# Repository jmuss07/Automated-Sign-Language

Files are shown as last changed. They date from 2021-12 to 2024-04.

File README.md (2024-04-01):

# Automated Sign Language

## Table of Contents

- [Phase 1](#phase-1)
- [Phase 2](#phase-2)
- [Phase 3](#phase-3)
- [About Us](#about-us)

## Phase 1

Goals, Planning, etc.

**Description**: A robotic, anthropomorphic hand that can display the ASL alphabet and basic one-handed gestures.

**Test of Success**: Through the hand, using the ASL alphabet, a word can be transmitted, received, and interpreted in under two minutes.

**Proof of Concept**: [ASLAN robot](https://www.hubs.com/blog/theres-not-enough-sign-language-translators-so-these-students-3d-printed-a-humanoid-robot/) made by Uni. of Antwerp students.

Components of Antwerp:

- 16 servos
- 25 3D printed parts (139 hour print time)
- 3 motor controllers
- Arduino Due
- 10 hour assembly time
- Access to global database

| Recreatable | Unrealistic |
| --- | --- |
| Arm is 3D printed | 16 servos |
| Roughly human size | Able to learn |
| Multiple parts that assemble into the whole | Access to constantly updated local network of global signs |
| Finger and arm joints move individually | Network connected users can send messages that the hand interprets |

### What We Don't Know

- How to make a moveable finger joint.
- Typed input into letters, into hand sign. What's the process? (Library of servo movements? for each letter?).
- Turn speech into text that can be then inputted.
- Some signs and gestures require either unnatural movement, or a more complex process.
  - The signs for "z" and "j" require excessive movement of the arm.
  - Thumbs-up and thumbs-down require arm rotation.
  - etc.

### What We Need to Learn

- How to take audio (of speech), and turn it into a string interpretable by a microcontroller.
  - Speech-to-text (on raspberry pi?)
  - Parse and turn text into individual letters.
  - Turn the individual letters into commands for each part of the hand.
- How a synthetic joint can be controlled by a servo motor.
  - Finger joint(s)
  - Wrist! It has multiple directions of movement irl!
- How to use a raspberry pi (as a speech-to-text server) in coordination with an arduino (as a microcontroller).
  - USB out on raspi (raspberry pi) to arduino?
  - Pins on raspi to arduino?
  - etc?

### Work Delegation

| Category | Josie | Henry |
| --- | ----- | ----- |
| Speech-to-text | 65% | 35% |
| Finger & Wrist control | 35% | 65% |

_Note: These numbers and divisions are pretty arbitrary._

### Timeline

| Date  | Goal |
| ----- | --- |
| 12/17 | Planning finished, box & arm modeled, hand & stt (speech-to-text) started |
| 1/7 | Box finished, arm in final revisions, servo/hand issue solved, rudimentary stt established |
| 1/14  | Arm finished, hand being developed with servos, stt able to trigger servo |
| 1/21  | Hand being printed/in final revisions, full project assembled, stt finished |
| 1/28  | Physical project finished, troubleshooting |
| 2/4 | Final documentation finished, project submitted |

### Estimated Cost

| Item | Cost per Item | Quantity | Total Cost |
| --- | --- | --- | --- |
| Servo | $5.95 | 8 | $47.60 |
| 3D Printer Model Material | $2.43 / in³ | 8 in³ | $19.44 |
| 3D Printer Support Material | $4.76 / in³ | 1.5 in³ | $7.14 |
| 1/8" Acrylic Sheet | $2.65 / ft² | 9.5 ft² | $25.18 |
| Wire | $0.08 / ft | 6 ft | $0.48 |
| Panel-mount SPDT Switch | $0.95 | 1 | $0.95 |
| LED (Green or Red) | $0.16 | 1 | $0.16 |
| Arduino Uno/Metro | $24.95 | 1 | $24.95 |
| Arduino Prototyping Shield  | $11.49 | 1 | $11.49 |
| Raspberry Pi | $35.00 | 1 | $35.00 |
| | | **Final Estimated Cost**: | $172.39 |

Yes, this estimated cost is rather high. However, a lot of these materials are readily available already in the Sigma Lab, and can be re-used for future projects. If need be, $75 is available to purchase extra materials.

_Thanks to [Sigma Lab Wiki](http://wiki.chssigma.com/index.php?title=Sigma_Lab_Equipment_Costs) for the numbers._

### Parts and Uses

| Part | Use |
| --- | --- |
| Microphone | To pick up speech as audio. |
| Raspberry Pi | To run a speech-to-text server, and turn the audio into strings, and the strings into commands sent to the arduino. |
| Arduino | To control the servos. |
| Switch | To turn the whole unit on and off. |
| Arm Servos | To rotate the arm, and bend the wrist. |
| Hand Servos  | To control the individual fingers on the hand. |
| Elastic | To let the hand servos bend/extend the fingers on the hand. |

### Safety

- The base box will be made of acrylic, and have the weight of the arm on it. If any point has too much stress, the acrylic could break. This would cause sharp edges, so there's **danger of cuts**.
- If the whole arm will be able to rotate, and the fingers/wrist move quick, then there will be a lot of fast movement. If parts are not secured properly, there could be a **risk of parts flying off and hurting someone**.
- As the physical interaction with the arm would be minimal, the **risk for electrical shock is low**.
  **soldering**
- We will need to solder various wires, which has the **risk of fire and burns** if the soldering iron is not used correctly.

### Images

A basic sketch for how the tension of the front of the arm may look...

FrontOfArm

...And a similar sketch for the back of the arm!

BackOfArm

_Credit to [Benton House](https://github.com/jhouse53) for the arm._

## Phase 2

Milestone work (From research, to final work)

The OpenBionics Lab's ADA v1.1 hand has designs for exactly what we're doing. But, it's designed for different servos, and a custom PCB. If we use anything from it, adaptations need to be made.

[ADA v1.1 Datasheet](Images/Ada_v1_1_Datasheet.pdf)

[Open Bionics Lab](https://openbionicslabs.com/downloads)

Below, is documentation of a single makeshift finger. Designed with minimal 3D printing, so manufacturing time is low. Overall, the only 3D-printed parts are the dowels, which take all of 10 minutes.

Finger Video:

https://user-images.githubusercontent.com/71345201/172168732-d8e445a4-d9d3-42a7-b983-bf6e3092c325.mp4

Box Video:

https://user-images.githubusercontent.com/71345201/172168760-eeb97748-df77-4b64-b599-513adac0ddce.mp4

Now, it's time to move onto the design of the final hand. The ADA v1.1 hand is made of a lot of Ninjaflex, too much for our project's budget. The final phase 2 goal is to cut this down.

So, it seems that the files provided by Open Bionics Labs were meshes, which Onshape does not support the editing of. The next best option is to either print the entire hand as-is, or re-design the fingers. The re-design would use the original .stl files as reference.

[Mesh Issues Video](Videos\2022-02-25_MeshIssues-mp4.mp4)

## Phase 3

Phase 3 is the combination and culmination of our work on the hand, string interpretation, and multi-servo control. As of now, this will not be achieved by the February 25th deadline. February 25th 2022, which at the time of writing, is today.

That was written over 2 months ago. Now, work starts again. At the moment, we have the fingers printed! Turns out, the Blender files (included with the ADA v1.1 download) were editable. This means a much higher chance of completing this project.

But before we get into that, lets take a break from all of this CAD to talk about the coding side of the project!
 Code Video Part 1:
 
 [Josie Stuff 1 Video](/Videos/2022-03-01_JosieStuff-mp4.mp4)
 
 Code Video Part 2:
 
 [Josie Stuff 2 Video](/Videos/2022-03-01_JosieStuff-2-mp4.mp4)
 
**ASL_Functions (Code Library):**
```python
import board
import neopixel
import pwmio
import servo

dot = neopixel.NeoPixel(board.NEOPIXEL, 1)
dot.brightness = 0.1

def full_up(servoToActuate):
    servoToActuate.angle = 0
def full_down(servoToActuate):
    servoToActuate.angle = 180
def half_fold(servoToActuate):
    servoToActuate.angle = 90
def full_palm(servoToActuate):
    servoToActuate.angle = 180
def half_palm(servoToActuate):
    servoToActuate.angle = 90
def pointed_out(servoToActuate):
    servoToActuate.angle = 0
def half_out(servoToActuate):
    servoToActuate.angle = 45

pwm1 = pwmio.PWMOut(board.D3, duty_cycle=2**15, frequency=200)
pwm2 = pwmio.PWMOut(board.D4, duty_cycle=2**15, frequency=200)
pwm3 = pwmio.PWMOut(board.D5, duty_cycle=2**15, frequency=200)
pwm4 = pwmio.PWMOut(board.D6, duty_cycle=2**15, frequency=200)
pwm5 = pwmio.PWMOut(board.D7, duty_cycle=2**15, frequency=200)

thumb = servo.Servo(pwm1)
pointer = servo.Servo(pwm2)
middle = servo.Servo(pwm3)
ring = servo.Servo(pwm4)
pinky = servo.Servo(pwm5)

def neutral():
    full_up(thumb)
    full_up(pointer)
    full_up(middle)
    full_up(ring)
    full_up(pinky)

def sign_a():
    full_up(thumb)
    full_down(pointer)
    full_down(middle)
    full_down(ring)
    full_down(pinky)
    print("A")

def sign_b():
    full_palm(thumb)
    full_up(pointer)
    full_up(middle)
    full_up(ring)
    full_up(pinky)
    print("B")

def sign_c():
    half_out(thumb)
    half_fold(pointer)
    half_fold(middle)
    half_fold(ring)
    half_fold(pinky)
    print("C")

def sign_d():
    full_palm(thumb)
    full_up(pointer)
    full_down(middle)
    full_down(ring)
    full_down(pinky)
    print("D")

def sign_e():
    full_palm(thumb)
    half_fold(pointer)
    half_fold(middle)
    half_fold(ring)
    half_fold(pinky)
    print("E")

def sign_f():
    half_fold(thumb)
    half_fold(pointer)
    full_up(middle)
    full_up(ring)
    full_up(pinky)
    print("F")

def sign_g():
    full_up(thumb)
    full_up(pointer)
    full_down(middle)
    full_down(ring)
    full_down(pinky)
    print("G")

def sign_h():
    full_up(thumb)
    full_up(pointer)
    full_up(middle)
    full_down(ring)
    full_down(pinky)
    print("H")

def sign_i():
    half_fold(thumb)
    full_down(pointer)
    full_down(middle)
    full_down(ring)
    full_up(pinky)
    print("I")

def sign_j():
    half_fold(thumb)
    full_down(pointer)
    full_down(middle)
    full_down(ring)
    full_up(pinky)
    print("J")

def sign_k():
    full_up(thumb)
    full_up(pointer)
    full_up(middle)
    full_down(ring)
    full_down(pinky)
    print("K")

def sign_l():
    pointed_out(thumb)
    full_up(pointer)
    full_down(middle)
    full_down(ring)
    full_down(pinky)
    print("L")

def sign_m():
    full_palm(thumb)
    half_fold(pointer)
    half_fold(middle)
    half_fold(ring)
    full_down(pinky)
    print("M")

def sign_n():
    full_palm(thumb)
    half_fold(pointer)
    half_fold(middle)
    full_down(ring)
    full_down(pinky)
    print("N")

def sign_o():
    half_fold(thumb)
    half_fold(pointer)
    half_fold(middle)
    half_fold(ring)
    half_fold(pinky)
    print("O")

def sign_p():
    full_up(thumb)
    full_up(pointer)
    half_fold(middle)
    full_down(ring)
    full_down(pinky)
    print("P")

def sign_q():
    full_up(thumb)
    full_up(pointer)
    full_down(middle)
    full_down(ring)
    full_down(pinky)
    print("Q")

def sign_r():
    half_palm(thumb)
    full_up(pointer)
    full_up(middle)
    full_down(ring)
    full_down(pinky)
    print("R")

def sign_s():
    half_palm(thumb)
    full_down(pointer)
    full_down(middle)
    full_down(ring)
    full_down(pinky)
    print("S")

def sign_t():
    full_up(thumb)
    half_fold(pointer)
    full_down(middle)
    full_down(ring)
    full_down(pinky)
    print("T")

def sign_u():
    half_palm(thumb)
    full_up(pointer)
    full_up(middle)
    full_down(ring)
    full_down(pinky)
    print("U")

def sign_v():
    half_palm(thumb)
    full_up(pointer)
    full_up(middle)
    half_fold(ring)
    full_down(pinky)
    print("V")

def sign_w():
    half_palm(thumb)
    full_up(pointer)
    full_up(middle)
    full_up(ring)
    full_down(pinky)
    print("W")

def sign_x():
    full_palm(thumb)
    half_fold(pointer)
    full_down(middle)
    full_down(ring)
    full_down(pinky)
    print("X")

def sign_y():
    pointed_out(thumb)
    full_down(pointer)
    full_down(middle)
    full_down(ring)
    full_up(pinky)
    print("Y")

def sign_z():
    full_palm(thumb)
    full_up(pointer)
    full_down(middle)
    full_down(ring)
    full_down(pinky)
    print("Z")

def sign_0():
    half_out(thumb)
    half_fold(pointer)
    half_fold(middle)
    half_fold(ring)
    half_fold(pinky)
    print("0")

def sign_1():
    pointed_out(thumb)
    full_down(pointer)
    full_down(middle)
    full_down(ring)
    full_down(pinky)
    print("1")

def sign_2():
    full_palm(thumb)
    full_up(pointer)
    full_up(middle)
    full_down(ring)
    full_down(pinky)
    print("2")

def sign_3():
    pointed_out(thumb)
    full_up(pointer)
    full_up(middle)
    full_down(ring)
    full_down(pinky)
    print("3")

def sign_4():
    full_palm(thumb)
    full_up(pointer)
    full_up(middle)
    full_up(ring)
    full_up(pinky)
    print("4")

def sign_5():
    pointed_out(thumb)
    full_up(pointer)
    full_up(middle)
    full_up(ring)
    full_up(pinky)
    print("5")

def sign_6():
    full_palm(thumb)
    full_up(pointer)
    full_up(middle)
    full_up(ring)
    full_down(pinky)
    print("6")

def sign_7():
    full_palm(thumb)
    full_up(pointer)
    full_up(middle)
    half_fold(ring)
    full_up(pinky)
    print("7")

def sign_8():
    full_palm(thumb)
    full_up(pointer)
    half_fold(middle)
    full_up(ring)
    full_up(pinky)
    print("8")

def sign_9():
    half_fold(thumb)
    half_fold(pointer)
    full_up(middle)
    full_up(ring)
    full_up(pinky)
    print("9")

asl_dict = {
    "a": sign_a,
    "b": sign_b,
    "c": sign_c,
    "d": sign_d,
    "e": sign_e,
    "f": sign_f,
    "g": sign_g,
    "h": sign_h,
    "i": sign_i,
    "j": sign_j,
    "k": sign_k,
    "l": sign_l,
    "m": sign_m,
    "n": sign_n,
    "o": sign_o,
    "p": sign_p,
    "q": sign_q,
    "r": sign_r,
    "s": sign_s,
    "t": sign_t,
    "u": sign_u,
    "v": sign_v,
    "w": sign_w,
    "x": sign_x,
    "y": sign_y,
    "z": sign_z,
    "0": sign_0,
    "1": sign_1,
    "2": sign_2,
    "3": sign_3,
    "4": sign_4,
    "5": sign_5,
    "6": sign_6,
    "7": sign_7,
    "8": sign_8,
    "9": sign_9,
}

```
**Parser Code:**
```python
import time
from ASL_functions import asl_dict, neutral

cont = False
while not cont:
    neutral()
    phrase = input("\nPlease enter a phrase, or type -q to quit: ").lower()
    if phrase == "-q":
        cont = True
    else:
        confirm = input(f"\nIs '{phrase}' correct? (Y/N)\t")
        if confirm.lower() == "y":
            print()
            for i in phrase:
                print(i)
                if i not in asl_dict:
                    print(f"Sorry, I don't know how to sign {i}")
                else:
                    asl_dict[i]()
                    time.sleep(1)
            neutral()
```
Now then! Back to the CAD work!

Printed Fingers

_Update 2022-05-13_: I (Henry) am currently trying to design a frame for the hand, to replace what we cut off of the model in Blender.

_2022-06-03_: It's been a minute, or two, or almost a month since the last update. It's been rough. Here's the penultimate video:

[Penultimate Video](/Videos/2022-06-03_Penultimate-mp4.mp4)

### Josie's Reflection

As the school year draws to a close, so too does our project. Though we haven't fully completed it, we got extremely close, which, for such a complex project, is impressive. Throughout the experience, I've built on my pre-existing code skills. I've learned how to make and use code libraries of my own, for isntance! At times, the project _would_ get frusturating. However, I managed to get past the challenges by taking brealks, looking at things differently, and asking for advice and feedback from those around me.

### Henry's Reflection

So, this is the last day of Engineering for the 2021-2022 school year. I have some things to say.

- Despite not finishing, I am _extremely_ proud of what I did this year. Last year, my project was nowhere near this finished.

- I made this design way too small and detailed. Half of the laser-cut pieces (the frame) snapped, and half of the 3D printed pieces (the finger joints) printed incorrectly.

- Bad documentation hurts you when you need to come back to the project after a break.

- Problem solving really helps, problem avoiding never does.

- When something's going wrong, and you just want to quit: Do it. Take a break, calm down, and come back at a different angle.

## About Us

### **Josie Muss**

Hey there! I'm Josie, and I'm currently a student at Cal Poly, and graduated from Charlottesville High School class in 2023. This repository documents a project done in 2022 (my Junior year of high school). You can find more of my projects on my [Github](https://github.com/jmuss07). Any questions for me on either this project or any of others that I've worked on can be sent to me at [jmuss@calpoly.edu](mailto:jmuss@calpoly.edu).

### **Henry Heisig**

Hi! I'm Henry, a class of 2024 student at Charlottesville High School. You can contact me at [hheisig51@charlottesvilleschools.org](mailto:hheisig51@charlottesvilleschools.org) or [henry+github@eheisig.com](mailto:henry+github@eheisig.com), or find my work on [Github](https://github.com/hheisig51).

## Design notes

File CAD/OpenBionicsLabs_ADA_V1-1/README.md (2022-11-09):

---
nav_exclude: true
---
# Ada_3D_model_files

This folder contains the design files for the Ada hand. 
The Ada hand is named after Ada Lovelace, "the first computer programmer". 
This hand is not a prosthesis, it is intended as a development kit. 
Components such as the circuit board and motors are available for purchase soon from www.openbionics.com

This work is licensed under the Creative Commons Attribution-ShareAlike 4.0 International License.
To view a copy of this license, visit http://creativecommons.org/licenses/by-sa/4.0/
org.

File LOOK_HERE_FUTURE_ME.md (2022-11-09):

# what we were doing at the end of the year
- realized that the servos and the arduino can't both be on the inside because they'll tear each other apart
- servo mounting holes are too close together (also true on the servo model‽)
- sometimes the wires come out of the servo connectors
- do the servos even have enough articulation to move the elastic the full distance?
- use wires to fish elastic through fingers
- finger monuts are too thin
- current fingers should probably be reprinted (hopefully on the prusas)
- use proper mounting hardware this time instead of superglue

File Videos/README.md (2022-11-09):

# Videos

A collection of videos recorded for documentation.

[Box Video](Videos\2022-02-09_Box-mp4.mp4)

[Finger Video](/Videos/2022-02-09_Finger-mp4.mp4)

[Ninjaflex Hand Video](/Videos/2022-02-14_NinjaflexHand-mp4.mp4)

[Mesh Issues Video](/Videos/2022-02-25_MeshIssues-mp4.mp4)

[Josie Stuff 1 Video](/Videos/2022-03-01_JosieStuff-mp4.mp4)

[Josie Stuff 2 Video](/Videos/2022-03-01_JosieStuff-2-mp4.mp4)

[Penultimate Video](/Videos/2022-06-03_Penultimate-mp4.mp4)

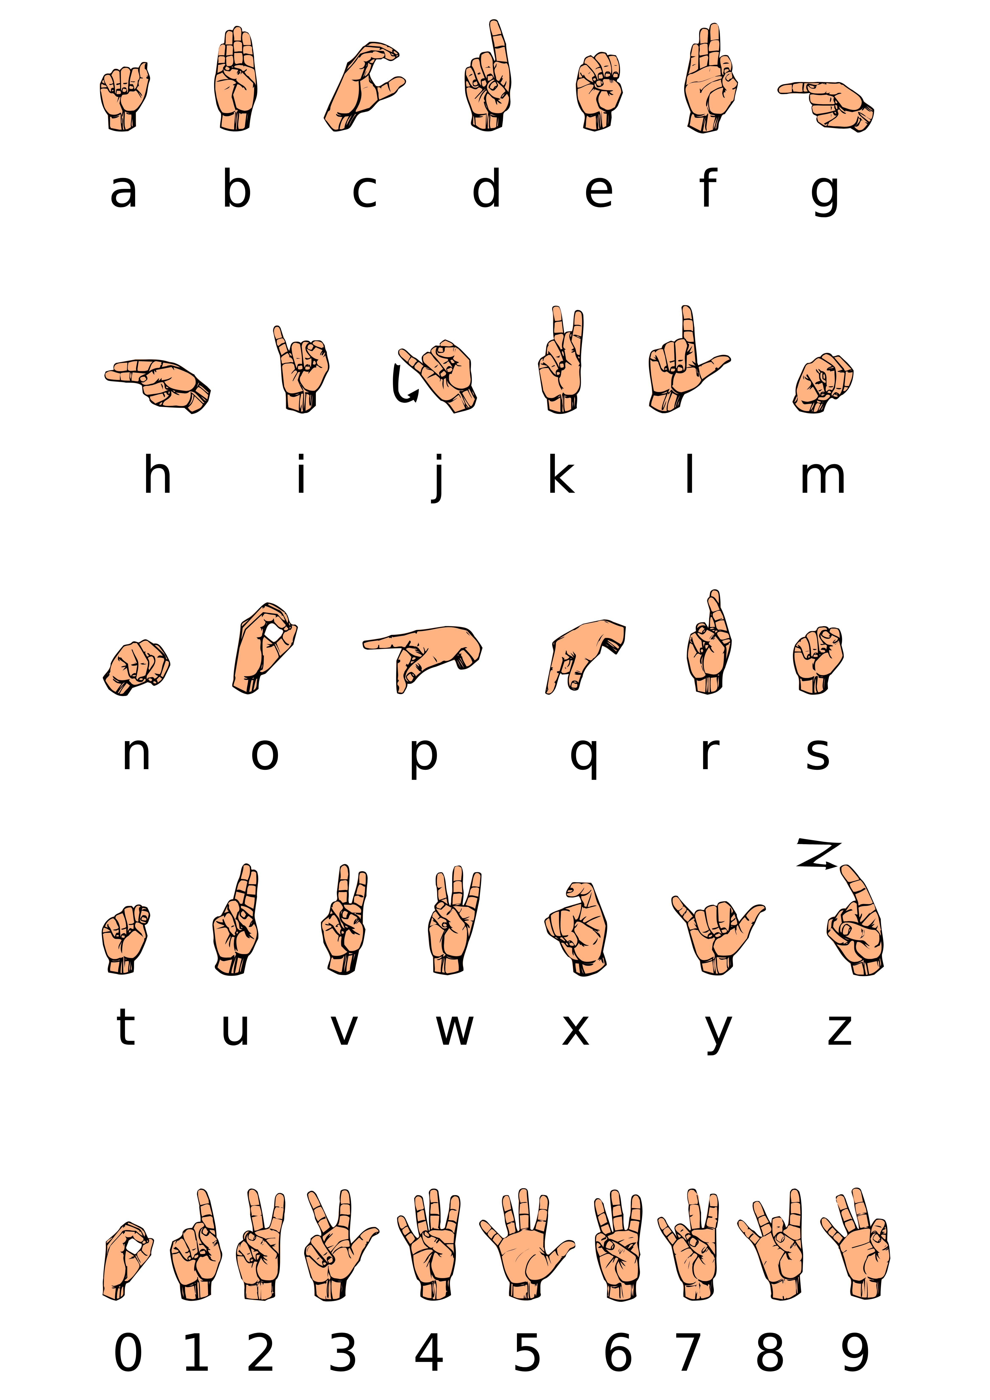
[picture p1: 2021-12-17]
Images/ASL_Chart.png

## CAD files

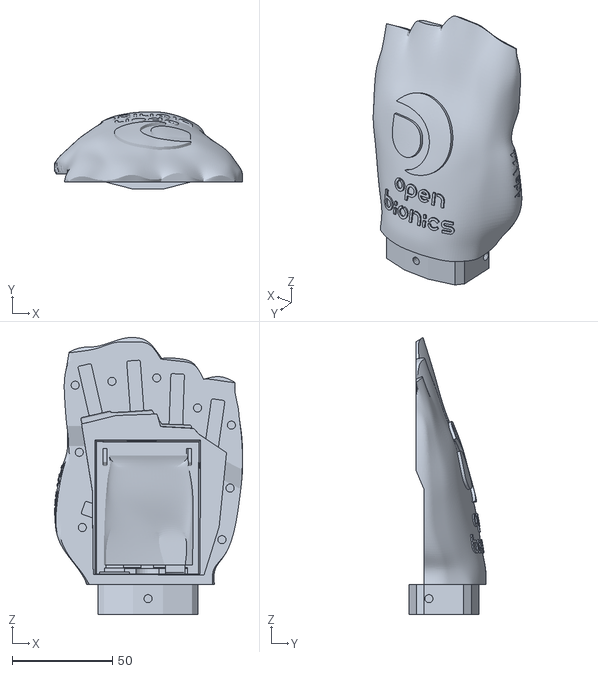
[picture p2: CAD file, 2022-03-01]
CAD/OpenBionicsLabs_ADA_V1-1/STLs/Left Hand/L_Ada_v1.1_Back_Cover.stl
94.1 x 38.6 x 138.3

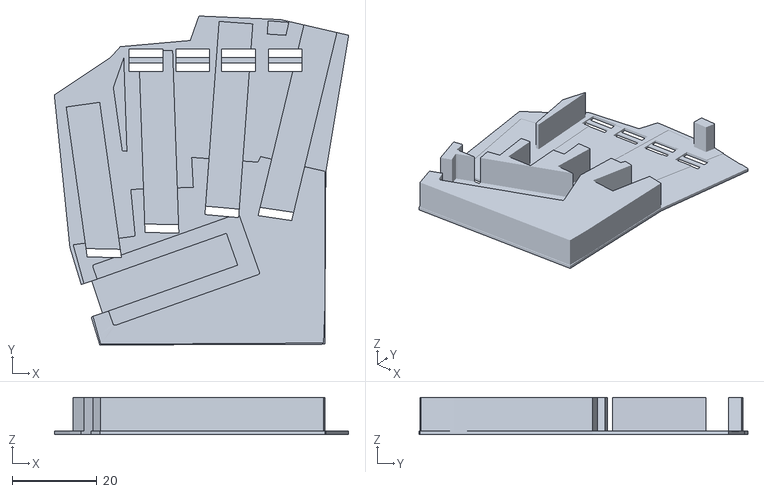
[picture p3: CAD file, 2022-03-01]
CAD/OpenBionicsLabs_ADA_V1-1/STLs/Right Hand/R_Ada_v1.1_PCB_Tray_Lower.stl
69.6 x 77.8 x 8.82

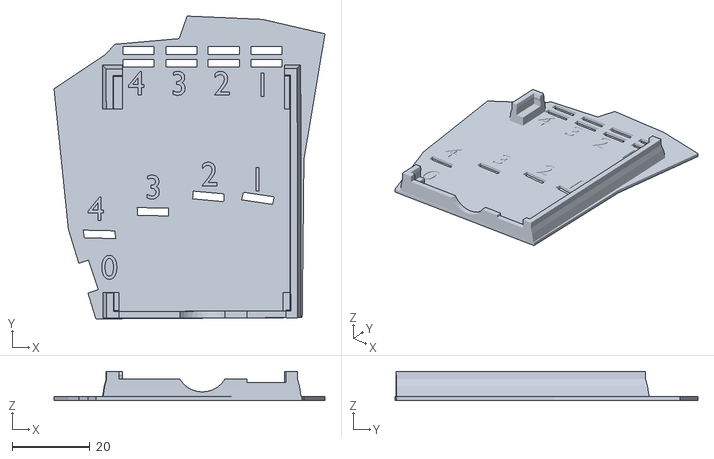
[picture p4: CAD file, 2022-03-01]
CAD/OpenBionicsLabs_ADA_V1-1/STLs/Left Hand/L_Ada_v1.1_PCB_Tray_Upper.stl
69.6 x 77.8 x 7.50

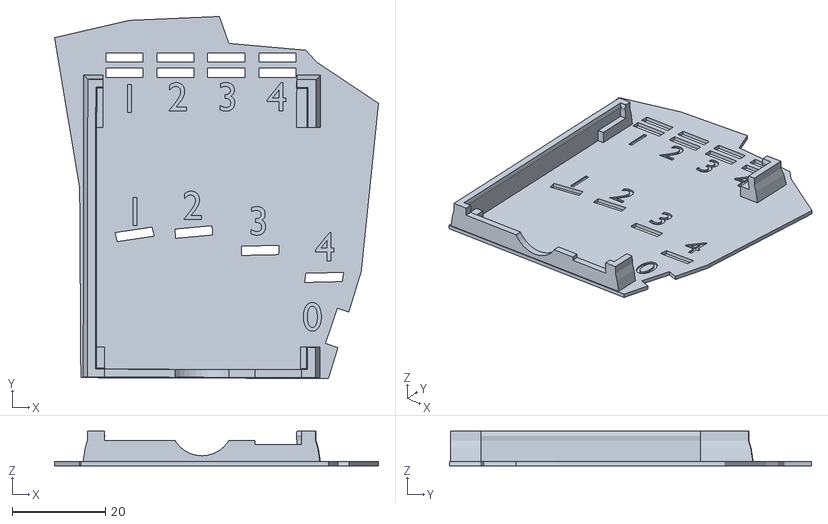
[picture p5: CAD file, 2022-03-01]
CAD/OpenBionicsLabs_ADA_V1-1/STLs/Right Hand/R_Ada_v1.1_PCB_Tray_Upper.stl
69.6 x 77.8 x 7.41

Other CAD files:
CAD/OpenBionicsLabs_ADA_V1-1/STLs/Left Hand/L_Ada_v1.1_PCB_Tray_Lower.stl
CAD/OpenBionicsLabs_ADA_V1-1/STLs/Right Hand/R_Ada_v1.1_Back_Cover.stl

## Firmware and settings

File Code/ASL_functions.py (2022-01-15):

def sign_a():
    print("Placeholder to sign the letter 'A'.")
    
def sign_b():
    print("Placeholder to sign the letter 'B'.")
    
def sign_c():
    print("Placeholder to sign the letter 'C'.")
    
def sign_d():
    print("Placeholder to sign the letter 'D'.")
    
def sign_e():
    print("Placeholder to sign the letter 'E'.")
    
def sign_f():
    print("Placeholder to sign the letter 'F'.")
    
def sign_g():
    print("Placeholder to sign the letter 'G'.")
    
def sign_h():
    print("Placeholder to sign the letter 'H'.")

def sign_i():
    print("Placeholder to sign the letter 'I'.")

def sign_j():
    print("Placeholder to sign the letter 'J'.")
    
def sign_k():
    print("Placeholder to sign the letter 'K'.")

def sign_l():
    print("Placeholder to sign the letter 'L'.")

def sign_m():
    print("Placeholder to sign the letter 'M'.")

def sign_n():
    print("Placeholder to sign the letter 'N'.")

def sign_o():
    print("Placeholder to sign the letter 'O'.")

def sign_p():
    print("Placeholder to sign the letter 'P'.")

def sign_q():
    print("Placeholder to sign the letter 'Q'.")

def sign_r():
    print("Placeholder to sign the letter 'R'.")

def sign_s():
    print("Placeholder to sign the letter 'S'.")

def sign_t():
    print("Placeholder to sign the letter 'T'.")

def sign_u():
    print("Placeholder to sign the letter 'U'.")

def sign_v():
    print("Placeholder to sign the letter 'V'.")

def sign_w():
    print("Placeholder to sign the letter 'W'.")

def sign_x():
    print("Placeholder to sign the letter 'X'.")

def sign_y():
    print("Placeholder to sign the letter 'Y'.")

def sign_z():
    print("Placeholder to sign the letter 'Z'.")

def sign_0():
    print("Placeholder to sign the letter '0'.")

def sign_1():
    print("Placeholder to sign the letter '1'.")

def sign_2():
    print("Placeholder to sign the letter '2'.")

def sign_3():
    print("Placeholder to sign the letter '3'.")

def sign_4():
    print("Placeholder to sign the letter '4'.")

def sign_5():
    print("Placeholder to sign the letter '5'.")

def sign_6():
    print("Placeholder to sign the letter '6'.")

def sign_7():
    print("Placeholder to sign the letter '7'.")

def sign_8():
    print("Placeholder to sign the letter '8'.")

def sign_9():
    print("Placeholder to sign the letter '9'.")

asl_dict = {
    "a":sign_a,
    "b":sign_b,
    "c":sign_c,
    "d":sign_d,
    "e":sign_e,
    "f":sign_f,
    "g":sign_g,
    "h":sign_h,
    "i":sign_i,
    "j":sign_j,
    "k":sign_k,
    "l":sign_l,
    "m":sign_m,
    "n":sign_n,
    "o":sign_o,
    "p":sign_p,
    "q":sign_q,
    "r":sign_r,
    "s":sign_s,
    "t":sign_t,
    "u":sign_u,
    "v":sign_v,
    "w":sign_w,
    "x":sign_x,
    "y":sign_y,
    "z":sign_z,
    "0":sign_0,
    "1":sign_1,
    "2":sign_2,
    "3":sign_3,
    "4":sign_4,
    "5":sign_5,
    "6":sign_6,
    "7":sign_7,
    "8":sign_8,
    "9":sign_9,
}

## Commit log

2022-01-10 Fixed parser.py issue with parsing spaces
    [ASL_functions.py, parser.py]
2022-01-11 Delete .markdownlint.json
    Only neccessary on local device.
2022-02-17 Added .stl of hands
    [L_Ada_v1.1_Back_Cover.stl, L_Ada_v1.1_PCB_Tray_Lower.stl, L_Ada_v1.1_PCB_Tray_Upper.stl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]
2022-02-18 Added some .stl
    [1.ply, 3.stl]
2022-02-18 Added 4.stl
    [4.stl]
2022-02-18 hi again
    [6.stl]
2022-02-25 Organized files, added videos
    [1.ply, 3.stl, 4.stl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]
2022-02-25 Added CAD documentation. Testing mp4 support
2022-03-28 FINALLY FIXED FINGERS
    [2022-03-28_Heisig_0th_Thumb.stl, 2022-03-28_Heisig_1st_finger.stl, 2022-03-28_Heisig_2nd_finger.stl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]
2022-05-17 Added Printing
    [2022-05-17_Pin_Henry-Heisig.stl, 2022-05-17_Thumb-Frame_Henry-Heisig.stl, 2022-05-17_Thumb-Plate_Henry-Heisig.stl]
2022-05-18 Modified site title
    [2022-05-17_Thumb-Base_Henry-Heisig.stl, 2022-05-17_Thumb-Plate_Henry-Heisig.stl]
2022-06-03 File structure revamp
    [1.ply, 2022-03-28_Heisig_0th_Thumb.stl, 2022-03-28_Heisig_1st_finger.stl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]
2024-04-01 Updated about me for Josie Muss to make it current
